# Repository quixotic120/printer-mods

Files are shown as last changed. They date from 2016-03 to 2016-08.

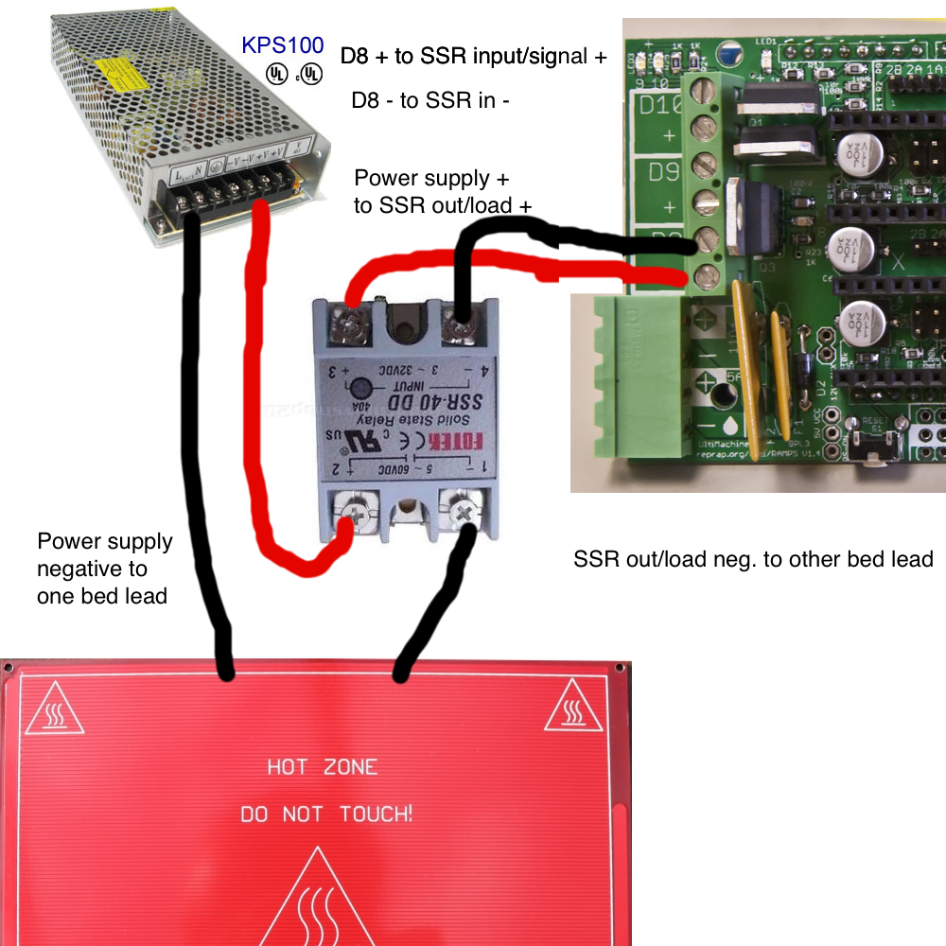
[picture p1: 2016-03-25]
SSR/SSR wiring.png

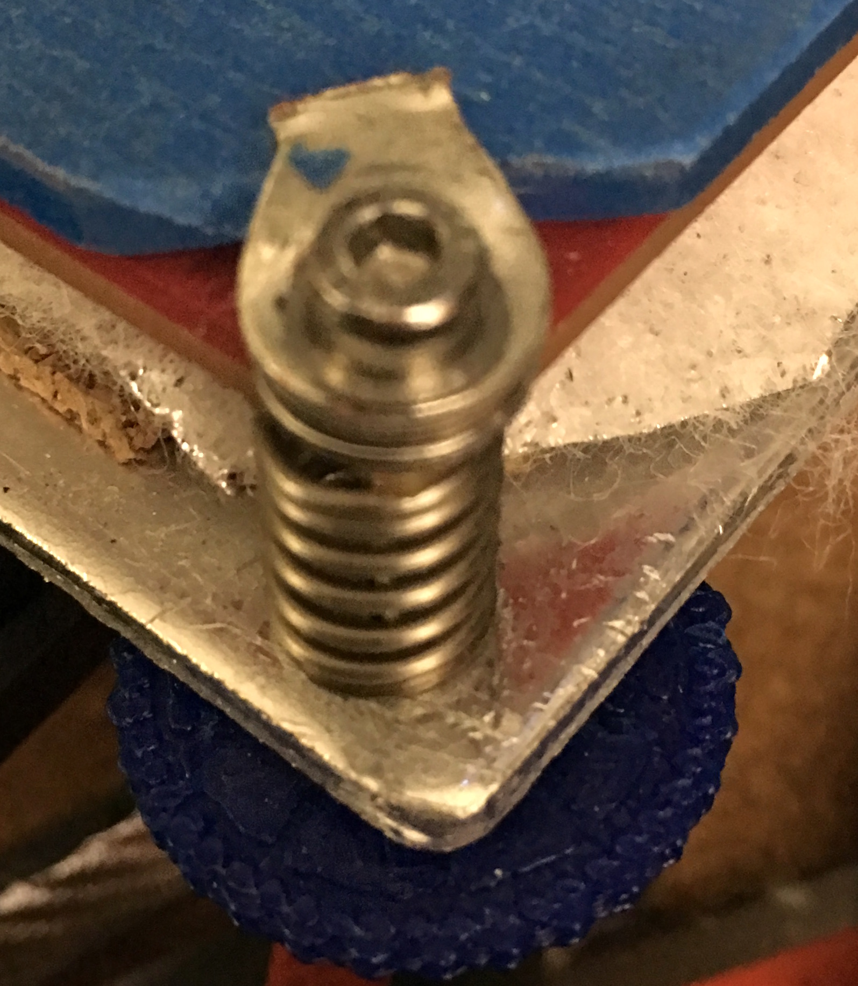
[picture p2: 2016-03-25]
bed clips/bed clamp.JPG

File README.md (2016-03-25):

**Detailed above:**

Bed clips - modified and cheap bed clip to maximize printable area

Fan shroud - fan shroud for dual e3d on the pegasus with one 40mm fan

SSR - using a solid state relay with the heated bed to enable PID temp control

endstops - basic structural mods to stiffen the end stops up and make them more consistent. 

Power supply - wiring a switch and fuse in as well as a case and mounts

electronics - making my own! see ramps-fd3 branch 

**Other mods I've done that are either basic or covered better elsewhere:**

Auto bed level - I basically followed [Zennmasters guide](http://zennmaster.com/random-things/auto-bed-leveling-for-the-makerfarm-prusa-i3-part-1-assembly-and-basic-setup). His STLs won’t work; I dont have an STL for my servo mount; I used colin's STL for the laser cut wood bit under the extruder along with the servo mount from [here](http://www.thingiverse.com/thing:735410/) . I didn't edit them, I just lay them on top of each other in my slicer until it looked right. Not the most reliable method but it worked well and was easy! the z-arm from that will be way too short though - there's a longer one on thingiverse but I found it too long. it's a fairly simple mesh so I had no problem turning it into a solid with 123D and stretching it to my preference but I accidentally deleted the STL after I printed. sorry! My z-arm about 58mm long - I would say you need a minimum of 52mm for this machine and that would be cutting it very close.
edit: trialing the differential IR endstop by dc42 - making my own, see sensorboard branch for kicad files

Lighting - not worth posting; literally just wired a few white LEDs to a switch and tapped the power supply, added a small perf board for constant 12V connection which I use for the lighting and the extruder fans. 

RAMPS fan - [simple mount for 80mm fan](http://www.thingiverse.com/thing:806125). You need two of them; I just wired it directly to 12v so it’s always on.

octopi - got a raspberry Pi zero by total dumb luck at micro center. Octopi is fairly simple and there are plenty of guides out there so I won’t cover it. I will say the following though: you need a nightly build for the zero as wheezy will not boot, the edimax ew-7811Un wifi adapter works well and is 10 bucks shipped on amazon, and wireless networks that have emoji in the SSID will not work with the autoconfig. 

Also if you need to diagnose an issue and can’t get ssh you can easily wire composite video as described [here](http://raspberrypi.stackexchange.com/questions/38812/pi-zero-video-out-header). saves you like 10-20 bucks on a stupid weird HDMI cable you will probably never use again. My pi is wired to a usb voltage drop down converter I had for a car (12v-5v) so it can be connected directly to the 12v PSU; don’t want too much load on the RAMPS board.

Got a pi 3 - considering switching to this and driving a touchscreen to replace/supplement the crappy ramps LCD.

filament filter - [this is neat](http://www.thingiverse.com/thing:492067) but I’m not convinced that it actually does anything. It’s simple to print and takes like 10 minutes so whatever, why not!

wire management - using a ton of the plastic bits that fill the open channels on the extrusions plus a bunch of zip ties and spiral wrap. It's ugly but functional. Would love suggestions on this front.

**future plans**

camera for octopi + mount: I ordered [this] (http://www.amazon.com/gp/product/B00V8A6CSU?psc=1&redirect=true&ref_=oh_aui_detailpage_o04_s01) camera:
it’s a piece of garbage but its really cheap. It didn’t work when it arrived but when I cracked it open I found the red cable had lifted from the pad at the usb plug. To further confuse things it did power on and they were not using the correct color code. oh well. 

soldered it back and it works with an okay picture and very bright lighting. the cable was extremely long so I shortened it significantly, wired the dimmer (wheel pot) in-line, and removed the PCB for the dimmer connecting everything directly to the USB male end. The PCB was garbage; the red cable kept coming up because solder would release from the pad under the smallest bit of force and outside of the trimpot there were no components on it (even though it was like 3” long!). Worked without drivers or software on OS X so I’m hoping for similar results on the Pi. Just need to find time to set it up.
edit: camera worked but picture quality was weak and it was YUYV so processor usage was high; repurposed for another use (see pixmicro branch). Bought a logitech c310 for 25 bucks on sale - it has a kind of clip stand thing so I just drilled a hole in that and mounted it directly to the extrusions. 

Z axis screws: threaded rods are kind of crappy. inconsistent, loud, dirty, and not very straight. In the meantime I’ve printed [this z bracket](http://www.thingiverse.com/thing:769057). It’s not amazing but I prefer it to the makerfarm mount where the nut kept working itself out and messing up the extruder offsets.
I’m researching acme/lead screws and trying to determine if the cheap Chinese sets are worth the 30-50 bucks.
edit: [i got these](http://www.qtecstore.com/pages/leadscrew_nuts/8mm_leadscrew_nuts/8mm_395_leadscrew_nut2/page.html) coupled with [these](http://www.amazon.com/uxcell-5mmx8mm-Helical-Coupler-Coupling/dp/B00KHTVOEU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) and using [these](http://www.amazon.com/uxcell®-Inner-Linear-Shaft-Support/dp/B00AUBG3PA?ie=UTF8&psc=1&redirect=true&ref_=oh_aui_detailpage_o03_s00) as supports. Shipping took awhile but product quality was very good and within tolerable specs - easily sufficient for 3d printing. Certainly are better options but you'll spend quite a bit more for improvement that is, in my opinion, unneccessary for this application

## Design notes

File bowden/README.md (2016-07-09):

work in progress

working off of the ultimate-greg's-wade's-geared-extruder (thingiverse/thing:966579
combined with the "flexy mod" (thing:1089085) to improve performance with softer
filaments. I also plan to add a few of the features from the reloaded version
(thing: 18379) that AndrewBCN left out. 

going with bowden and there are also mounts for the e3d that make up for the removal
of 90% of the carriage. One has a servo mount and one has a print fan mount as well.

also using (thing:1025775) because it is handy!

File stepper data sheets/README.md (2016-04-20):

these aren't mods but they were a total pain in the butt to find so I figured I'd throw them up here
42BHH48-151K-24B is my stepper for the extruders - 4.2V 1.8deg 1.5A stepper
35BHH37W-099A-21 is my stepper for everything else - 2.7V 1.8deg 1.0A stepper

vref- I aim for 70% max current to ensure heat is under control and have not had issues

polulu a4988 - vref = tripmax * 8 * (0.05) = max 0.4 vref for 1.0A motors, 0.6 vref for 1.5A motors

DRV8825 - vref = tripmax/2 = max 0.5v for 1.0A, max 0.75v for 1.5A 

stepsticks - vref = tripmax * 1.6 = 1.6v for 1A - maxed out. can change s1,s2 to 0.1ohm, r1 to 30k, and remove and short r4 (or 0k replacement). this will raise max to 1.5A

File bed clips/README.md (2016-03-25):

borosilicate glass is available in 10”x10” sheets from McMaster-Carr (8476K21) - I scored the edges with a carbide drill bit, wet the score, and the bent the corner away with needle nose pliers. Not the cleanest break but it worked. Sanded lightly after but it didn’t really need it. A bit pricey but super flat and strong.

for the clamps search on thingiverse as there are printable clamps but if you have ring crimps and washers/don’t want a printed part on your hot bed read on

start with [ring crimp connectors](http://www.amazon.com/Shipping-Insulated-Connector-Electrical-Terminal/dp/B00FZK910K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).
I dont if these specific ones are good for this, I had some on hand that I had gotten locally. Try to find one that will fit under the M3 head. if not you can put a washer under the head like I did or get an M3 screw with a wider head. a tighter fit would probably be more effective but the added width of the larger crimp is handy. Luckily they’re dirt cheap!

cut off insulation and open crimp end with needle nose pliers. use cutting pliers to remove excess from crimp end, just enough to cross the edge of the glass 1-2mm or so. Bend the crimp end down slightly so it clamps harder.

place a spacer the size of your glass under the crimp. I used a stack of washers because I had a ton on hand and finding heat resistant spacers this small was difficult and/or too expensive to justify). for 3/32” plate glass a few washers will be tall enough, for my 1/8” (~3.175mm) borosilicate I used 4 M5 washers and it’s a touch too short but it works. If you can find a suitable spacer let me know and I’ll appreciate it. For the boro a spacer with 1/8” (~3.2mm) thickness, 1/8” (3.2mm) ID and 5/16” (8mm) to about 3/8” (9.5mm) OD. If the OD is much wider it won’t fit and it also has to be heat resistant to bed temps. I would say ~280F/140C to be safe.

In addition I add mini binder clips (~1/2”/13mm wide) in the spots where binder clips were. I don’t know how necessary this is but I did notice some gaps between the glass and the heated bed and these pulled it all together while taking up way less space than the ones you get from Makerfarm. 

optional: print and add [thumbwheels](http://www.thingiverse.com/thing:874155) to the M3 nuts. I think this is extremely helpful to set up the bed; even with auto bed leveling it should be trammed occasionally so that it’s as close as possible. 

With all of this you lose about 10mm from the edges which is way less than the original binder clips. I did this with stuff from my office and workshop so it was essentially free but even buying everything it should only be a few bucks. I noticed that Makerfarm has a printable upgrade that is basically a spacer at the end of the bed - this probably works fine as well but it requires an 11-12” length of glass. I was also wary to have a portion of the glass off the bed; uneven temperature distribution can weaken or break glass.

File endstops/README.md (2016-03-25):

very basic but made things a bit more consistent.

drilled out the holes on the limit switches to 3mm (I used 1/8”)- be careful with this as it’s fairly easy to crack the shell and ruin the switch. 

drilled out the zip tie holes on the wood to 3mm as well - I used a 7/64” (~2.7mm) bit so that it was a tight fit.

on the reverse of the wood I drilled the hole out with a countersink. I went until an M3 nut sat fairly flush.  

I only had M3x12 screws which were a touch long - I had extra nuts though so I just placed a second nut under the screw head, screwed through the switch into the wood and then into a nut on the opposite side. 

I found this held it in place much better than the zip tie. As you can see in the attached image I also removed the roller arm. I don’t know if this is necessary in X and Y but before I used ABL I found it was a noticeable improvement in the Z axis. If you do remove them in x and y (y especially) you have to be very careful to ensure the switches are able to triggered.

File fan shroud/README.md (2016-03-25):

fan shroud

had a heck of a time finding a replacement shroud for dual e3dv6. I broke both of the 30mm fans because they are kind of crappy. I had no 30mm fans on hand but I did have a 40mm. I found [this](http://www.thingiverse.com/thing:1065471/) which cools both with one 40mm fan and liked the design. Printed it and it was slightly too large but luckily he shared the IPT and I was able to modify to fit snugly. Still not sold on using one 40mm fan for both extruders but it appears to be as good as the two 30mm fans (still cool to the touch even when running 250C). Printed in ABS with 20% infill. The original STL prints fine but mine had some issues with the fins I added; you may have to play with it a bit. 

While I was at it I added a guard so I (hopefully) stop breaking fans. I like [this customizable one](http://www.thingiverse.com/thing:128718)

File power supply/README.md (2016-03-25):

Don’t have internal pics but can describe the process:

I used [this switch](http://www.amazon.com/gp/product/B00511QVVK?psc=1&redirect=true&ref_=oh_aui_detailpage_o05_s03) with a 10A fuse

looking at [the reverse of the switch](http://www.electro-tech-online.com/customimages/2011/10/2prtgk1-1.jpg) we can see 4 terminals on the switch at the top; label them as such:

1  |  2 
3  |  4

looking at the bottom E - labeled in green in the linked image - is earth and connected directly to earth on the PSU. N and L (black and white) connect to 2 and 4, then 1 and 3 would connect to N and L on the PSU side. 

I printed a random cover I found on thingiverse; can’t find it anymore. It’s slightly too wide anyway. The wires are loomed and come out of a hole; the cover had a bracket built into the loom hole that holds the wires in place with 2 M4 screws. It’s handy but if I were to remake this I would probably just socket the power wires. 

I printed [this mounting bracket](http://www.thingiverse.com/thing:46324). It probably works well; I ran out M4 screws which are what my power supply uses. it’ll happen someday.

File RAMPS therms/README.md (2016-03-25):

Change R1, R7, R11 to 1k instead of the 4.7K pull ups - should increase 
precision of thermistor readout and PID

haven't done this yet but plan to soon. will report on results when complete

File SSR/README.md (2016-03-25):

SSR + PID bed

Pros: 
more even heating of bed
less flex in bed
more precise temperature management
fairly simple

Cons:
Longer to heat up
a bit expensive

needs:
DC-DC solid state relay sufficient for your bed (10x10 makerfarm will need ~20 amps minimum)
heatsink for said relay and thermal paste
wire

connect d9 +/- to the SSR input
connect one lead of the bed directly to the power supply, note which polarity you use
connect the other polarity from the power supply to the positive on the SSR load end
connect the negative from the SSR load to the other bed lead. 
see wiring diagram.png

the bed is non-polar so it doesn’t matter which line from the power supply goes where. Just make sure that one polarity from the PSU goes directly to the bed and the opposite polarity goes to the SSR load and then the other bed lead.

some notes: [use cheap SSRs (Fotek, no name, counterfeit name brand, etc) from amazon and eBay at your own risk](http://canada.ul.com/safetyalerts/ul-warns-of-solid-state-relay-with-counterfeit-ul-recognition-mark-release-13pn-52/)

that being said, I’m using this [fotek SSR](http://www.amazon.com/gp/product/B019132BZS?psc=1&redirect=true&ref_=oh_aui_detailpage_o03_s01 obviously nowhere near its rated load (which I seriously doubt it could handle). it is working as expected and with a moderately sized heatsink maintains an acceptable temperature. YMMV depending on seller and batch though!

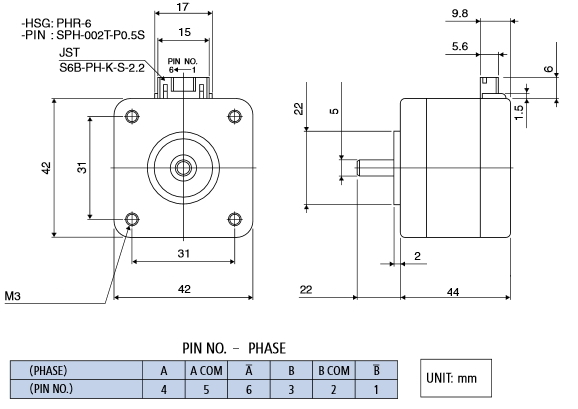
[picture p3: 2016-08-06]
stepper data sheets/Minebea_Astrosyn/sph-002t-p0.5s.png

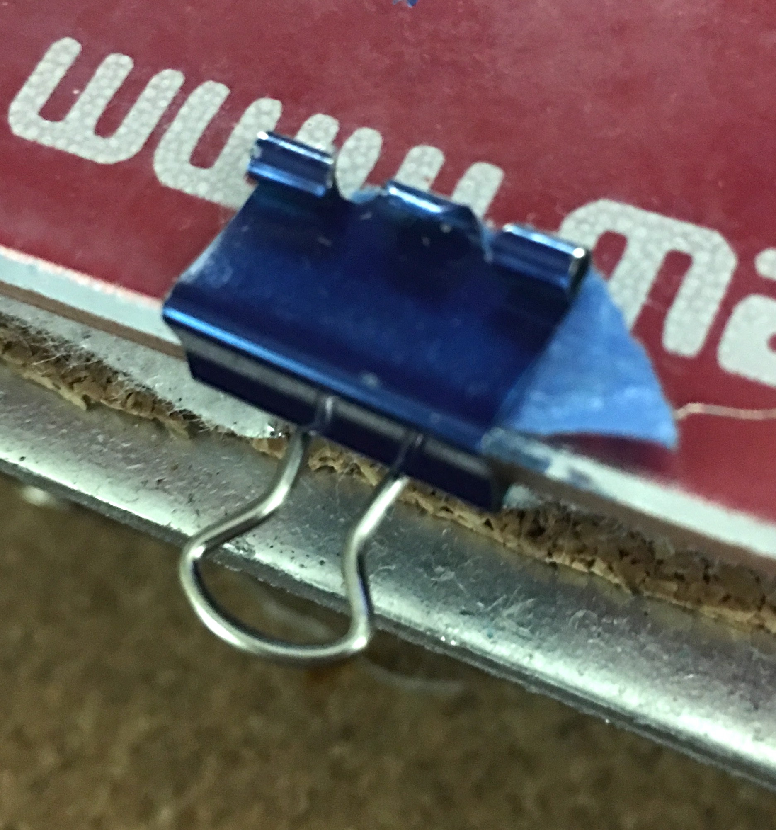
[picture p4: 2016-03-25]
bed clips/clip.JPG

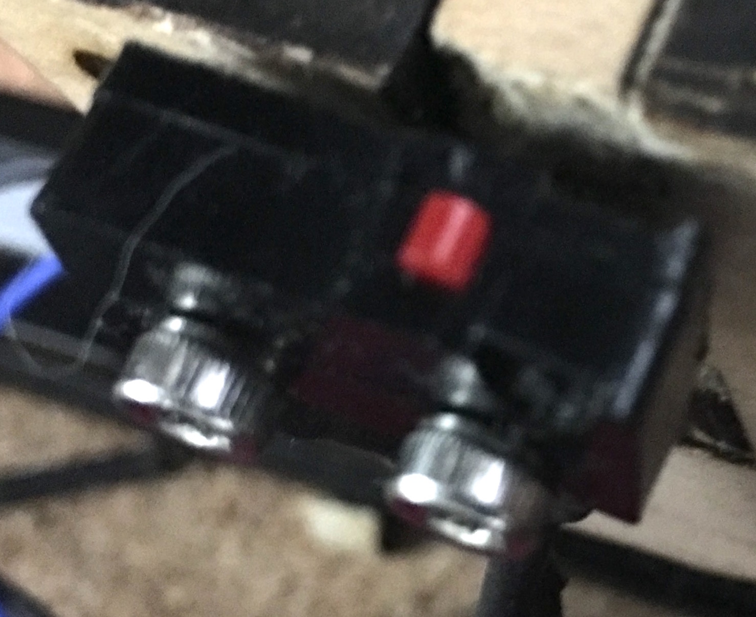
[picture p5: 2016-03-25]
endstops/zstop.JPG

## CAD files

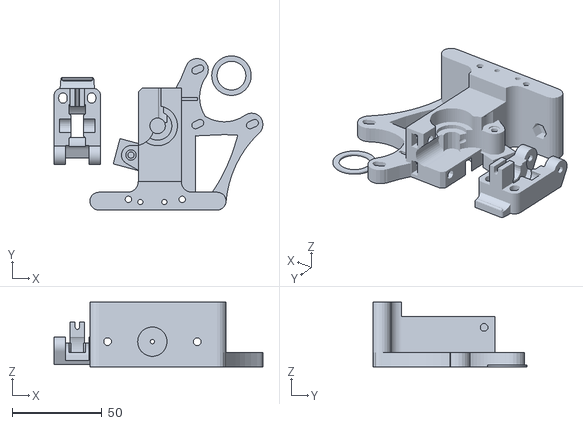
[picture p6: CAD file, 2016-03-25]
bowden/orig/ult-gregs-wades-30mm-v1_complete.stl
116.6 x 86.0 x 36.0

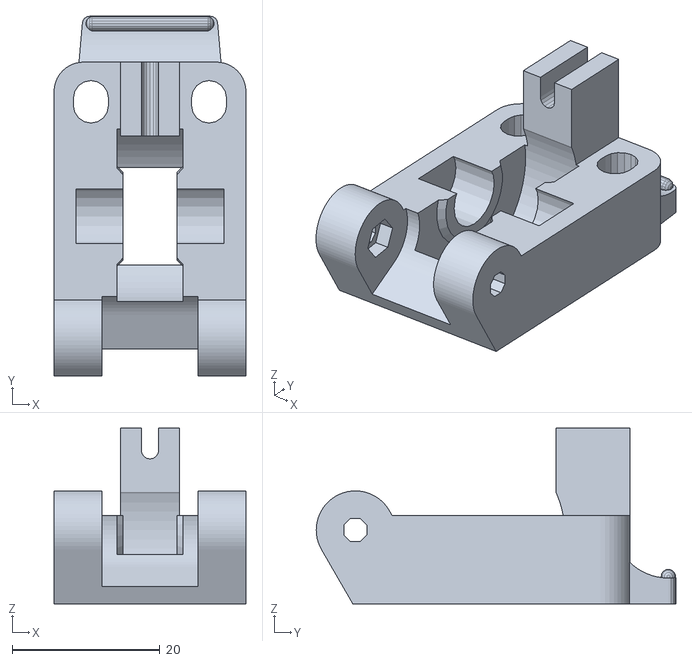
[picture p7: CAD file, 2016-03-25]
bowden/bowden mod/ult-gregs-wades-30mm-v1_guidler.stl
26.0 x 48.7 x 23.8

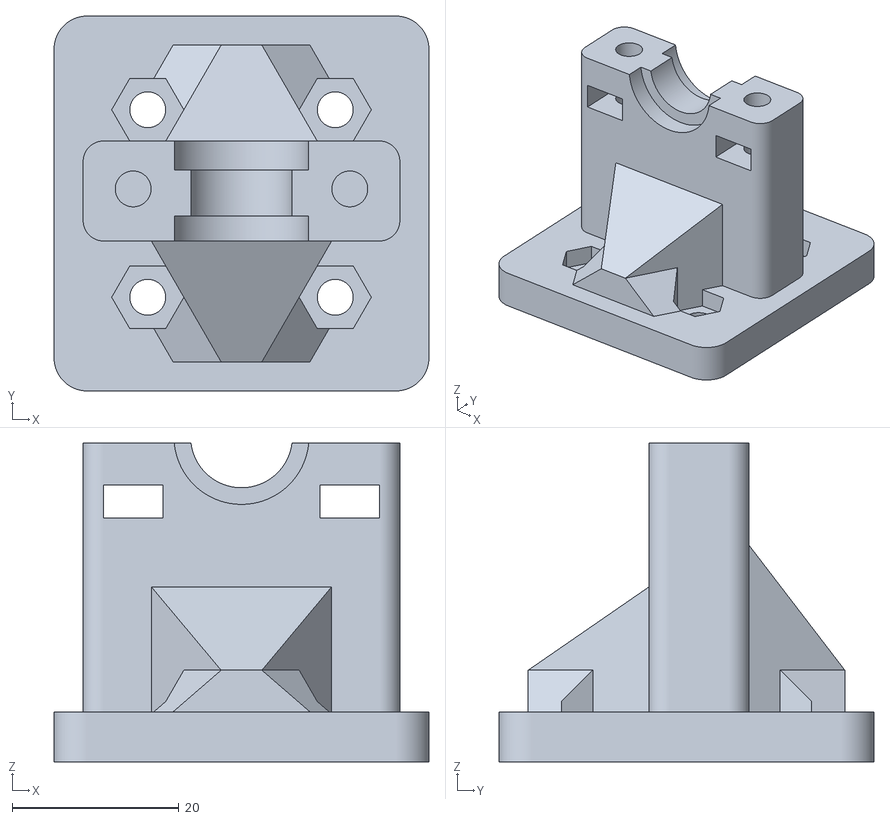
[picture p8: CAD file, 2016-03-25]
bowden/e3d mount/Bowden_carriage.stl
45.0 x 45.0 x 38.2

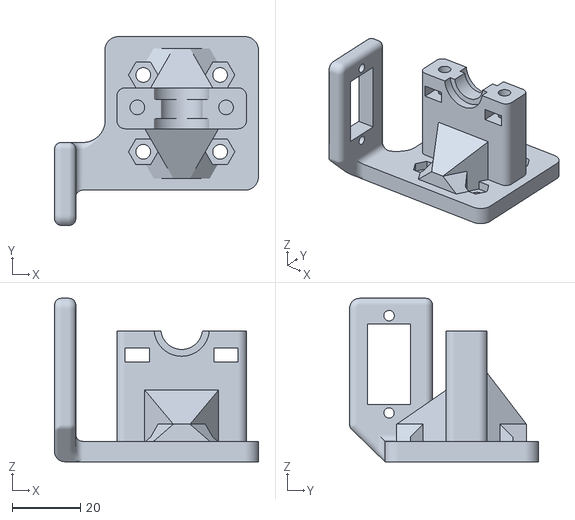
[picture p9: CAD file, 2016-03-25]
bowden/e3d mount/E3D_V6_Bowden_mount_with_servo./e3d_bowden_w_servo.stl
59.8 x 55.3 x 47.9

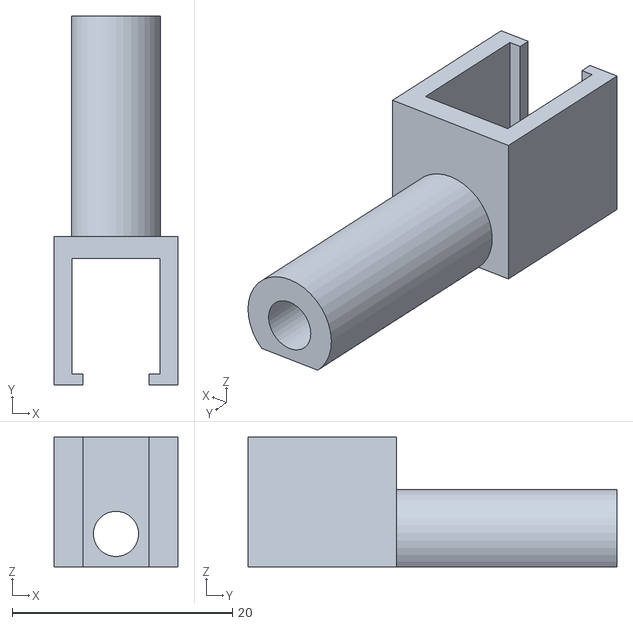
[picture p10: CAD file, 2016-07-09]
bowden/gregs_wade_align_fix.STL
11.3 x 33.5 x 11.8

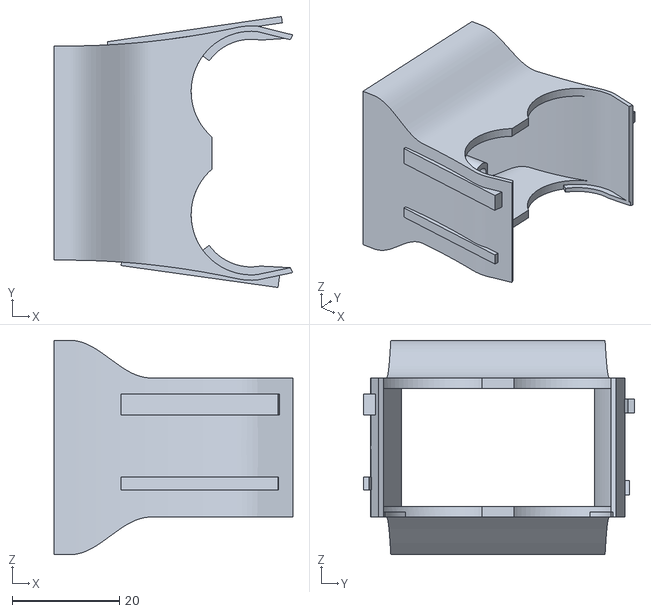
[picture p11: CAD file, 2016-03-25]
fan shroud/shroud.stl
44.5 x 50.6 x 40.0

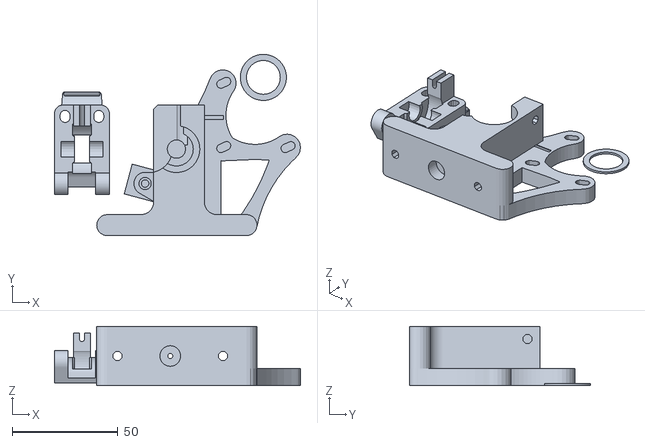
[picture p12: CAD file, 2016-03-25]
bowden/bowden mod/ult-gregs-wades-Bowden_base-v1.stl
116.6 x 85.9 x 28.0

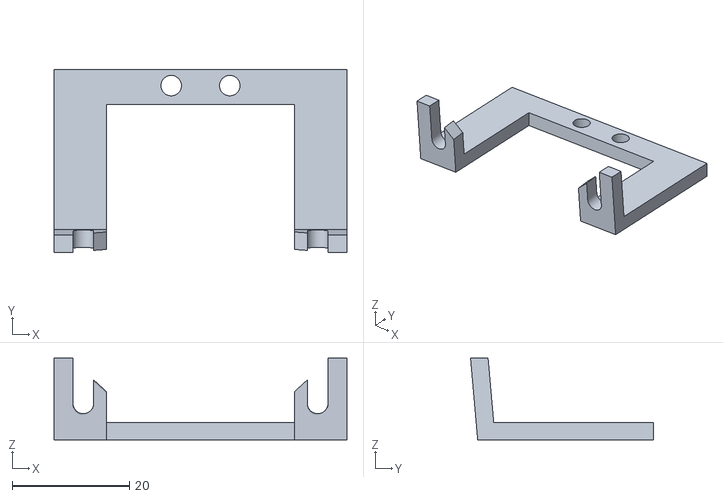
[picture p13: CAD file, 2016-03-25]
bowden/e3d mount/Bowden_carriage_clamp_50mmFanbracket.stl
50.0 x 31.2 x 14.0

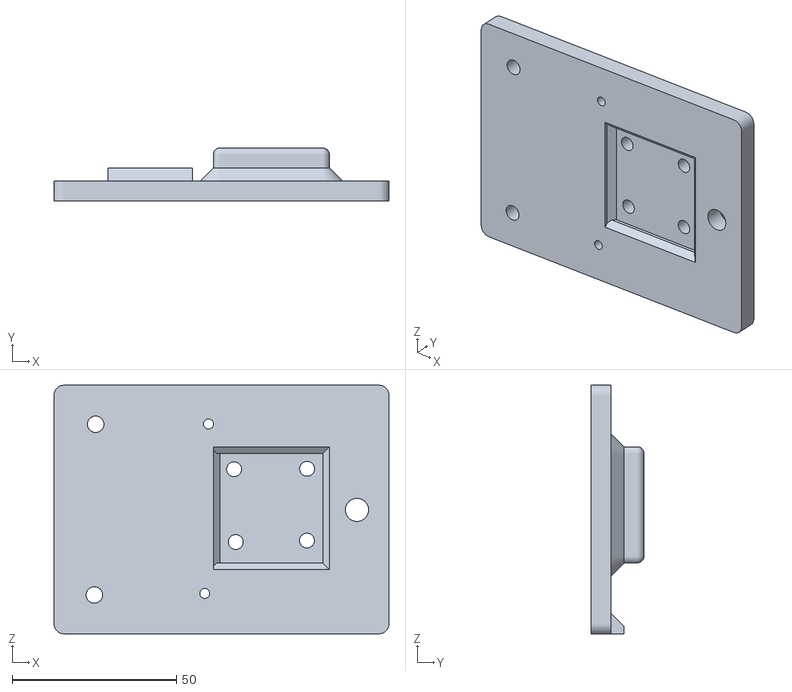
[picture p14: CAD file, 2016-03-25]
bowden/e3d mount/E3D_V6_Bowden_mount_with_servo./i3v_Conversion_bracket_1.stl
102.0 x 16.2 x 75.8

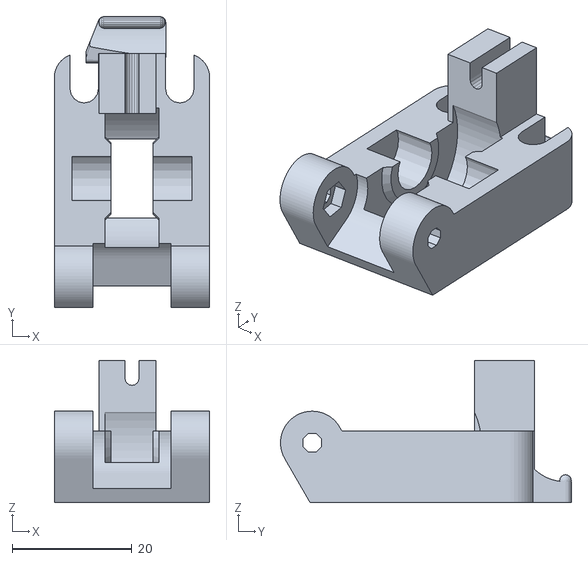
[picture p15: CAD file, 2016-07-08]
bowden/flexy mod w: bowden/guidler.stl
26.0 x 48.7 x 23.8

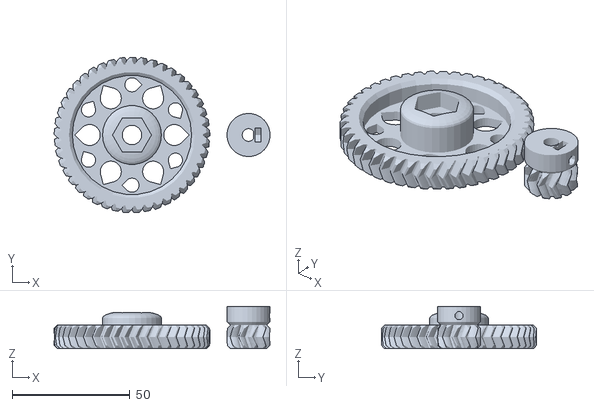
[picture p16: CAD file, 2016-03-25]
bowden/bowden mod/WadeHerringboneGears.stl
91.7 x 65.9 x 18.0

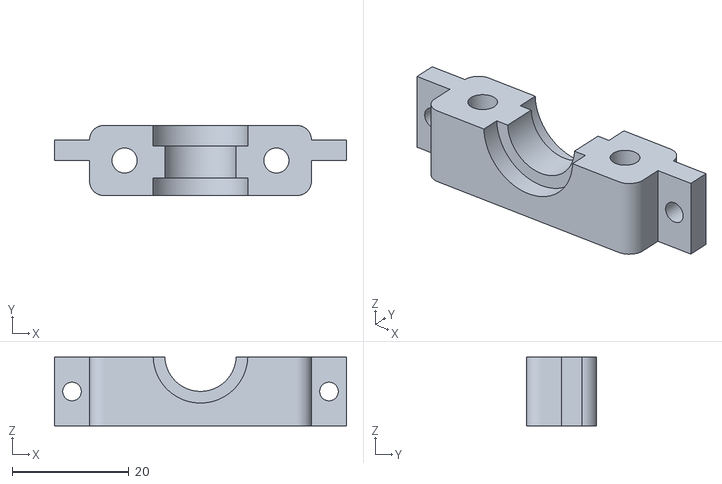
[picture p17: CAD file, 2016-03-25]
bowden/e3d mount/Bowden_carriage_clamp_FanMount.stl
50.0 x 12.0 x 11.8

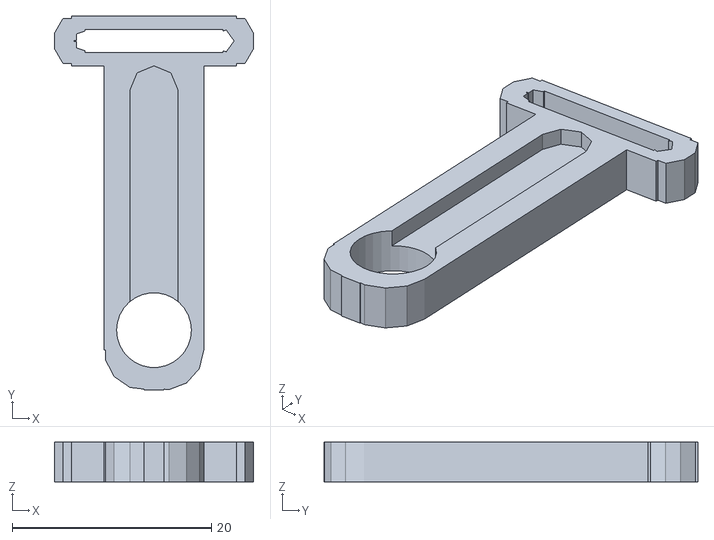
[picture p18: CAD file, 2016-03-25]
bowden/e3d mount/E3D_V6_Bowden_mount_with_servo./z-probe-endstop-holder.stl
20.0 x 37.5 x 4.00

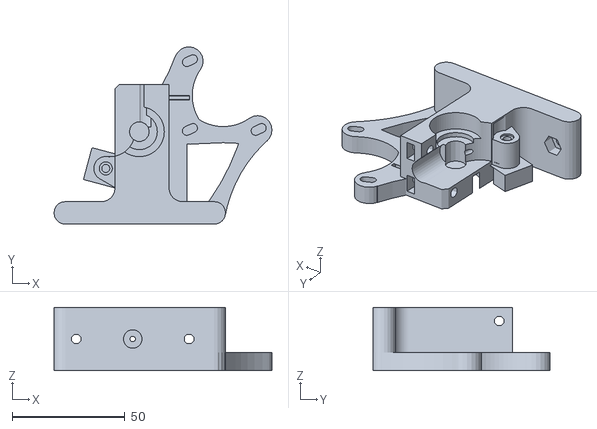
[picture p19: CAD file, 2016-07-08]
bowden/flexy mod w: bowden/ext_base.stl
96.6 x 78.6 x 28.0

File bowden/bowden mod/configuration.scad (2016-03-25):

// PRUSA iteration3
// Configuration file
// GNU GPL v3
// Josef Průša <josefprusa@me.com>
// Václav 'ax' Hůla <axtheb@gmail.com>
// http://www.reprap.org/wiki/Prusa_Mendel
// http://github.com/prusajr/PrusaMendel

// PLEASE SELECT ONE OF THE CONFIGURATIONS BELOW
// BY UN-COMMENTING IT

// Uncomment for metric settings
// METRIC METRIC METRIC METRIC METRIC METRIC METRIC METRIC 

include <metric.scad>;

// Custom settings here, tailor to your supplies and print settings

// Select your belt type ******************************************************

//T2.5
//belt_tooth_distance = 2.5;
//belt_tooth_ratio = 0.5;

//T5 (strongly discouraged)
//belt_tooth_distance = 5;
//belt_tooth_ratio = 0.75;

//HTD3
//belt_tooth_distance = 3;
//belt_tooth_ratio = 0.75;

//MXL
//belt_tooth_distance = 2.032;
//belt_tooth_ratio = 0.64;

//GT2
belt_tooth_distance = 2;
belt_tooth_ratio = 0.5;

// Choose bearing/bushing configuration ***************************************

//Choose from:

// 0 = Z as lm[e]8uu, X and Y bushings
// 1 = all bushings
// 2 = all bearings [default. Do not change unless you really know what you are doing]
// DO NOT OFFER 0 or 1 VARIANTS FOR SALE. We really mean that. In the long run it hurts everyone.

bearing_choice = 2;

// Bushing version
// 0 = square igus housings. By igus we mean JFM-0810-10 or GFM-0810-10
// 1 = round igus (works better if printed precisely)
// 2 = bronze self-aligning bushings
bushing_type = 0;

//Bearing version
// 0 = default lm8uu
// 1 = lme8uu
bearing_type = 0;

// Select idler bearing size **************************************************

// 0 = 608 [standard skate bearings]
// 1 = 624 [roughly same diameter as pulley, makes belt parallel so its prettier]

idler_bearing = 0;

// Thickness of the XZ plate board
board_thickness = 12;

//Layer height * width over thickness. Used for idler sleeve
single_wall_width = 0.3*2.2;

// END of custom settings


// You are not supposed to change this
board_to_xz_distance = 26;
xaxis_rod_distance = 45;
carriage_l = 74;
carriage_hole_to_side = 5;
carriage_hole_height = 4;

//calculated from settings

idler_size = (idler_bearing == 0) ? 22 : 13;

//use 4.5 for 608, 2.5 for 624
idler_size_inner_r = (idler_bearing == 0) ? 4.5 : 2.5;

idler_width = (idler_bearing == 0) ? 9 : 5;

// CHANGE ONLY THE STUFF YOU KNOW
// IT WILL REPLACE DEFAULT SETTING

// RODS

// threaded_rod_diameter = 0;
// threaded_rod_diameter_horizontal = 0;
// smooth_bar_diameter = 0;
// smooth_bar_diameter_horizontal = 0;

// Nuts and bolts

// m8_diameter = 0;
// m8_nut_diameter = 0;

// m4_diameter = 0;
// m4_nut_diameter = 0;

// m3_diameter = 0;
// m3_nut_diameter = 0;

// Bushing holder

// bushing_core_diameter = smooth_bar_diameter;
// bushing_material_thickness = 0;

///counted stuff
m3_nut_diameter_bigger = ((m3_nut_diameter  / 2) / cos (180 / 6))*2;

// functions
include <functions.scad>


// These constants define the geometry of the complete-printer.scad

//x_smooth_rod_length=325;
//y_smooth_rod_length=405;
//z_smooth_rod_length=235;
bed_x_size=225;
bed_y_size=225;

x_smooth_rod_length=450+board_thickness*2+10; // 492 for 16mm thickness; 484 for 12mm thickness
y_smooth_rod_length=470;
z_smooth_rod_length=405;  
bed_x_size=225;
bed_y_size=225;

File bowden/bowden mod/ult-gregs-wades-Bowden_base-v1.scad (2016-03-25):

// Ultimate Greg's Wade's Geared Extruder - Bowden version
// Licensed under the GNU GPLV3. 
// Copyright Greg Frost, 2010
// Various modifications to the original source code by various authors:
//
// - Jonas Kuehling (2012)
// - vlnofka (2012)
// - Misan (2013)
// - Marty Rice (2013)
// - AndrewBCN (August 2015)

// This version of Greg's Wade's Geared Extruder was designed to use with a Bowden
// filament system. Filament diameter is fixed at 1.75mm, because using 3mm filament
// with a Bowden system is not recommended.

// A mounting bracket is optional; check the basic bracket module at the end of the code.
// Note that using a bracket removes a lot of material from the base.

// AndrewBCN : I have included the OpenSCAD source code for the "fishbone" gears
// in separate files. You must pass the distance between axles (hobbed bolt and
// stepper) as a parameter.

// Assembly tip: use heat (e.g. a soldering iron) to insert the M3 nut in its nut trap in the idler.

///////////////////////////////////////////////////////////////////////////////////////////////////////////////////////

render_bracket = false; // select an extra mounting bracket or not

// Measure the Bowden pushfit connector you are using with a caliper.
// In my case, so these are the defaults:

bowden_pushfit_d = 9.6;      // Bowden pushfit diameter
bowden_pushfit_thread = 6.0; // Bowden pushfit thread length

// The Bowden connector will just be force-threaded into the base of the extruder.

///////////////////////////////////////////////////////////////////////////////////////////////////////////////////////

include<configuration.scad>
include<functions.scad>

// Define the hotend_mounting style you want by specifying hotend_mount=style1+style2 etc.
//e.g. wade(hotend_mount=groovemount+peek_reprapsource_mount);

bowden_mount=256;

// Make the default Bowden
default_extruder_mount=bowden_mount;

// Filament diameter
// - use 1.80 or 1.85 for 1.75mm diameter filament
filament_diameter=1.85;

// Base Extra Depth allows extra space for longer NEMA 17 steppers
// not used in this version, so value is zero.
base_extra_depth=0;

///////////////////////////////////////////////////////////////////////////////////////////////////////////////////////
// These variables are not used anymore

mounting_holes_legacy=1;
mounting_holes_symmetrical=2;
default_mounting_holes=mounting_holes_symmetrical;

///////////////////////////////////////////////////////////////////////////////////////////////////////////////////////
// Render the various parts
// AndrewBCN : I suggest printing them separately, so comment out
// the lines for the parts you don't want to print

// Extruder body
wade(hotend_mount=default_extruder_mount,mounting_holes=default_mounting_holes);

// Bearing Washer
translate([52,70,0]) bearing_washer();

// Guidler
translate([-20,0,15.25]) rotate([0,-90,0]) wadeidler();

///////////////////////////////////////////////////////////////////////////////////////////////////////////////////////
// Visualisation
// (disabled)

//color("red")
//x-carriage v2
//translate([24,-32.75,base_extra_depth+wade_block_depth]) 
  //rotate([0,0,0]) 
    //import("../output/x-carriageV2.stl");


//%translate([45.0, 55.50, 1]) //[46.78,55, 1]
//  rotate([0, 0, 0])
//    nema17(places=[0,1,1,1], holes=true, shadow=5);

/*
color("silver")
translate(large_wheel_translation) {
	translate([0,0,-15])import("../output/biggearmod_fixed.stl");
	rotate([0,0,29.5]) translate([gear_separation,0, 5]) {
		rotate([180,0,0]) import("../output/smallgearmod_fixed.stl");
		rotate([0,0,-29.5]) translate([0,0,-4]) {nema17(places=[0,1,1,1], holes=true, shadow=5, $fn=7, h=8);
		}
	}
}
*/
///////////////////////////////////////////////////////////////////////////////////////////////////////////////////////
/**
 * Extruder
 * @name Extruder
 * @assembled
 * @using 1 small-gear
 * @id extruder
 * @using 1 idler
 * @using 1 extruder-body
 * @using 1 m3nut
 * @using 1 m3washer
 * @using 1 m3x25
 * @step Take idler and insert nut into small nut-trap inside the hinge.
 * @step While holding the nut in place, preprare M3x25 bolt with washer and screw it into the hinge just enough to hold the nut.
 * @step Now take the extruder body and idler. Place idler on the hinge counterpart and compleately screw the M3x25 bolt. This will create secured hinge.
 * 
 * @using 2 m4nut
 * @step Place M4 nuts into their nut traps, secure them with piece of tape. We need them in place, since later they would be harder to access.
 * 
 * @using 3 m3x10
 * @using 3 m3washer
 * @using 1 NEMA17
 * @step Prepare your NEMA17 stepper motor and three M3x10 screws with washers.
 * @step Hold motor on place and lightly tighten the screws. We need to adjust motor position later, no need to tighten it hard.
 * 
 * @using 1 large-gear
 * @using 1 m8washer
 * @using 2 m8nut
 * @using 2 bearing-608
 * @step Place two skate bearings on ther position, they should snuggly fit in.
 * @step Insert prepared large gear into the body with mounted bearings.
 * @step Check if the alignment of hobbed part with the filament path. Adjust it accordingly with adding or removing M8 washers.
 * @step After adjusting, we need to fix the bolt in. So we place washer at the end of hobbed bolt and with two M8 nuts we will do locknut by tightening them against each other.
 * @step Check if large gear turns freely.
 * 
 * @using 2 m3x40
 * @using 4 m3washer
 * @using 2 extruder-spring
 * @step Prepare two M3x40 screws with sandwitch of washer-spring-washer.
 * @step Insert two M3 nuts into nut traps on top of drive mechanism. [[extruder/top-nut-traps.png]]
 * @step Insert prepared screws into the holes on idler. Close the idler and tighten the screws into the trapped nuts. More you tighten those screws, more pressure will be on fillament.
 * @step Your extruder is done. [[extruder/assembled.jpg]]
 */

/**
 * Extruder body
 * @name Extruder body
 * @category Printed
 * @id extruder-body
 */

/**
 * Extruder idler
 * @name Extruder Idler
 * @id idler
 * @category Printed
 * @using 1 bearing-608
 * @using 1 idler-m8-piece
 * @step Insert piece of M8 rod into bearing.
 * @step Insert 608 bearing with rod into printed idler part.
 */

/**
 * Small M8 rod 
 * @name Idler
 * @id idler-m8-piece
 * @category Rods and Bars
 */

/**
 * Spring used for idler on extruder.
 * @name Extruder spring
 * @id extruder-spring
 */

//===================================================
// Parameters defining the wade body:

elevation = 2; // AndrewBCN: was 15mm, decreased to 2mm for Bowden version
wade_block_height=55+elevation;
wade_block_width=24;
wade_block_depth=28;

block_bevel_r=6;

base_thickness=10;
base_length=70+2-6;
base_leadout=25+2+1-6;
//base_extra_depth=0; // commented out here since we defined it above

nema17_hole_spacing=1.2*25.4;//31; 
nema17_width=1.7*25.4;
nema17_support_d=nema17_width-nema17_hole_spacing;

screw_head_recess_diameter=7.2;
screw_head_recess_depth=3;

motor_mount_rotation=0;
motor_mount_translation=[48,50+elevation,0];
//motor_mount_translation=[52.5,38,0]; //original
motor_mount_thickness=8;

large_wheel_translation=[50.5-(7.4444+32.0111+0.25),34+elevation,0];

m8_clearance_hole=8.8;
hole_for_608=22.15; // AndrewBCN : was 22.3mm, decreased to 22.15mm
608_diameter=22;

block_top_right=[wade_block_width,wade_block_height];

layer_thickness=0.2; // AndrewBCN : 0.2mm recommended
filament_feed_hole_d=(filament_diameter*1.1)/cos(180/8);
hobbing_depth=2;
echo ("filament_feed_hole_d", filament_feed_hole_d);

//This is the distance from the centre of the filament to the centre of the hobbed bolt.
filament_feed_hole_offset=8/2-hobbing_depth+filament_diameter/2;

echo ("filament_feed_hole_offset", filament_feed_hole_offset);

idler_nut_trap_depth=7.5;
idler_nut_thickness=4;

gear_separation_tolerance=0.25;
gear_separation=7.4444+32.0111+gear_separation_tolerance;

echo ("distance between axles (excluding tolerance)", gear_separation-gear_separation_tolerance);

function motor_hole(hole)=[
	motor_mount_translation[0],
	motor_mount_translation[1]]+
	rotated(45+motor_mount_rotation+hole*90)*nema17_hole_spacing/sqrt(2);

// Parameters defining the idler.
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

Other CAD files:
bowden/bowden mod/ult-gregs-wades-Bowden_bracket-v1.stl
bowden/e3d mount/Bowden_carriage_clamp.stl
bowden/flexy mod w: bowden/big gear.stl
bowden/flexy mod w: bowden/smallgear.stl
bowden/bowden mod/WadeHerringboneGears.scad
bowden/bowden mod/functions.scad
bowden/bowden mod/involute_gears.scad
bowden/bowden mod/metric.scad
bowden/bowden mod/teardrop.scad
bowden/bowden mod/ult-gregs-wades-Bowden_bracket-v1.scad
bowden/flexy mod w: bowden/WadeHerringboneGears.scad
bowden/flexy mod w: bowden/WadeHerringboneGears.stl
bowden/flexy mod w: bowden/flexy-fixed-gregs-wades.scad
bowden/flexy mod w: bowden/flexy-fixed-gregs-wades.stl
bowden/flexy mod w: bowden/metric.scad
bowden/flexy mod w: bowden/teardrop.scad
bowden/flexy mod w: bowden/washer.stl
bowden/orig/metric.scad
bowden/orig/teardrop.scad
bowden/orig/ult-gregs-wades-30mm-v1.scad
bowden/orig/ult-gregs-wades-30mm-v1_washer.stl

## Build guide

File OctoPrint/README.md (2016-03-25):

very basic and ugly script to allow you to flash marlin from inside OctoPrint.

install avrdude (sudo apt-get install avrdude)
copy flash_marlin somewhere (I use ~/OctoPrint/scripts)
edit SOURCEDIR to reflect your username
edit MARLINHEX to reflect the name of your marlin hex file
make it executable (chmod +x)

edit config.yaml (sudo nano ~/.octoprint/config.yaml) and add the following to the system section:
  - action: flash
    command: ~/path/to/flash_marlin
    confirm: You are about to flash Marlin, ensure up-to-date hex is in SOURCEDIR
    name: Flash Marlin

restart octoprint or the computer

to use: scp marlin.hex into sourcedir, click system in octoprint, click flash, etc. Probably smart to run it from cli once to see output and make sure it’s working - I don’t know how to pass script messages to octoprint so if it fails it just does nothing (most situations it would just leave the octoprint service dead but I don’t know how well that works). If you get a port error you may need /ttyUSB0 instead of ACM0 - raspbian/octopi uses ACM0 but other releases use USB0. 

to make a hex file: 
on OS X preferences for arduino IDE 1.6.7 is /users/name/Library/Arduino15/preferences.txt
open and add line build.path=/Users/name/path/to/hex/output
save and restart IDE - compile/check and compilation will output to path established above. Use MFMarlin.ino.hex with above instructions assuming you’ve cloned my git. don’t use eep, elf, or with_bootloader.hex.

edit: added a line to flash eeprom_clear before flashing marlin. Was having issues with persistant EEPROM values between flashing. I generally hardcode all of my settings into firmware so this isnt a huge deal but if you don't you should comment out the line about eeprom_clear.hex. the eeprom_clear code is part of the arduino ide so you can grab it from the examples lib

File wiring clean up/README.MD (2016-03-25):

Wiring

any suggestions to improve here are greatly appreciated! I’ve cleaned it up quite a bit but it’s still a bit of a mess, especially around the RAMPS board.

some notes:
if you don’t have them get connector housings (listed as dupont connectors on a lot of sites or “rectangular connector housing”, just make sure it’s not keyed and has a 2.54mm pitch). Theres a ton of excess in the wiring that can be eliminated

https://www.grainger.com/product/80-20-T-Slot-Cover-16U368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 additional t-slot covers for extrusions

suggestions for wiring cleanup (directly at RAMPS board especially) are greatly appreciated

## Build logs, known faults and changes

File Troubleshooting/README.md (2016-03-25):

less documented fixes for issues I've encountered that were headaches:

no feed from extruder - check for blockage (manually feed filament with head at higher than typical temp), ensure nozzle and peek tube are attached correctly, ensure stepper voltage is correct (mine is around 0.48V), ensure the drive gear is attached sufficiently/not sliding around, etc

clicking from extruder - check stepper voltage, play with tension on extruder idler (less is more, playing with mod ideas for this next because it is a pain to set perfectly), check for partial blockage

inversion of axes during homing procedure - check that endstop logic is correct with M119 and invert in config.h if needed

abl ignores z-offset - ensure endstop logic is correct, ensure software endstops are off, check eeprom settings with M501 - if there is a z-offset in eeprom it supercedes firmware

adjusting stepper drivers - i have a small all metal eyeglass screwdriver that I alligator clip to my + MM probe, this way I can read the value as i adjust the voltage

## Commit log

2016-03-25 various mods for 3d printer
    [Bowden_carriage.stl, Bowden_carriage_clamp.stl, Bowden_carriage_clamp_50mmFanbracket.stl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]
2016-08-06 new steppers
